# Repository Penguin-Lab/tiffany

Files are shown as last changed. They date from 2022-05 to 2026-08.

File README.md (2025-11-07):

# tiffany
A Tiffany é uma hexapod desenvolvida para andar de forma autônoma ou para ser controlada pelo celular. Para se locomover, ela possui 6 patas de 3 graus de liberdade cada (3 motores) e uma ESP32 que comanda o conjunto! Ela é a segunda integrante robótica do nosso espaço inteligente!

# Estrutura física
A estrutura física do robô é composta por seis patas de três eixos cada (três motores). As patas são fixadas a duas placas de PLA para deixar o robô firme. As peças são todas projetadas em 3D e foram impressas utilizando PLA, podendo ser encontradas na pasta Pecas_3d deste projeto.

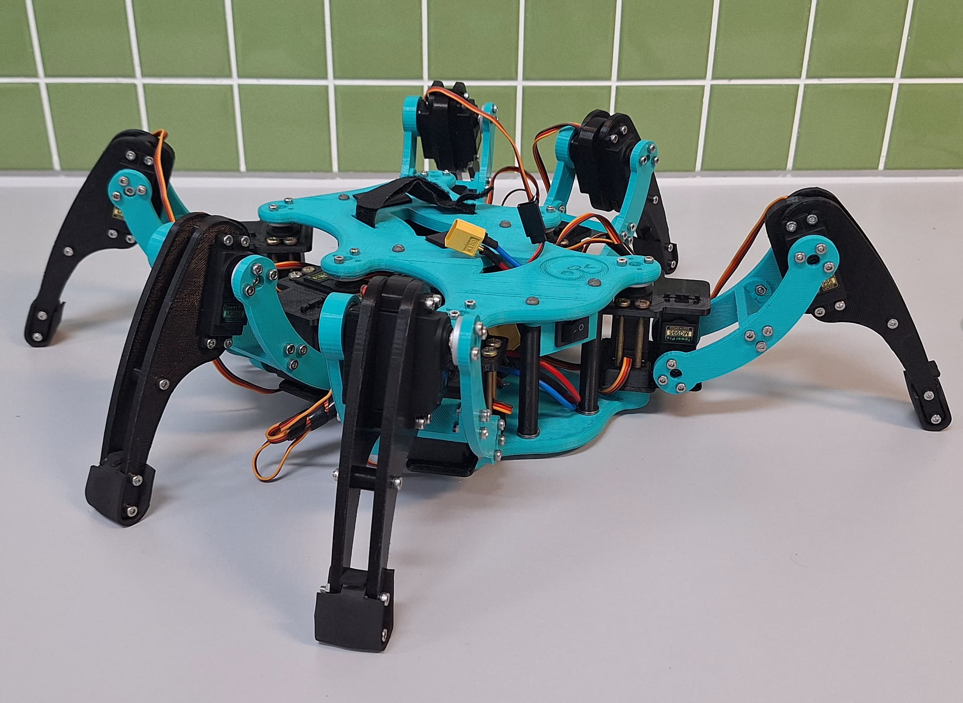
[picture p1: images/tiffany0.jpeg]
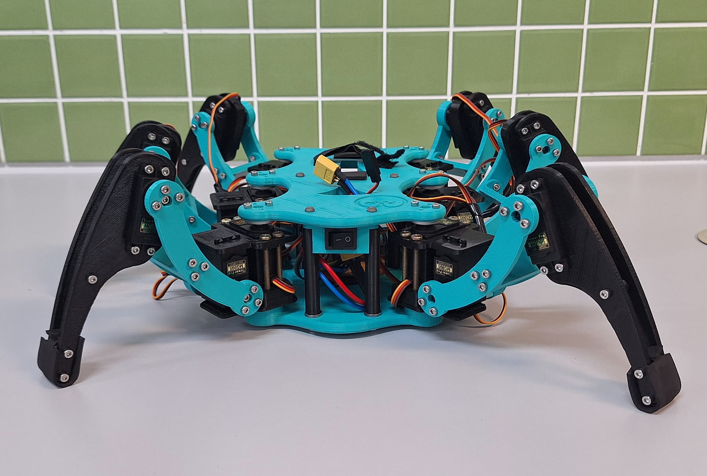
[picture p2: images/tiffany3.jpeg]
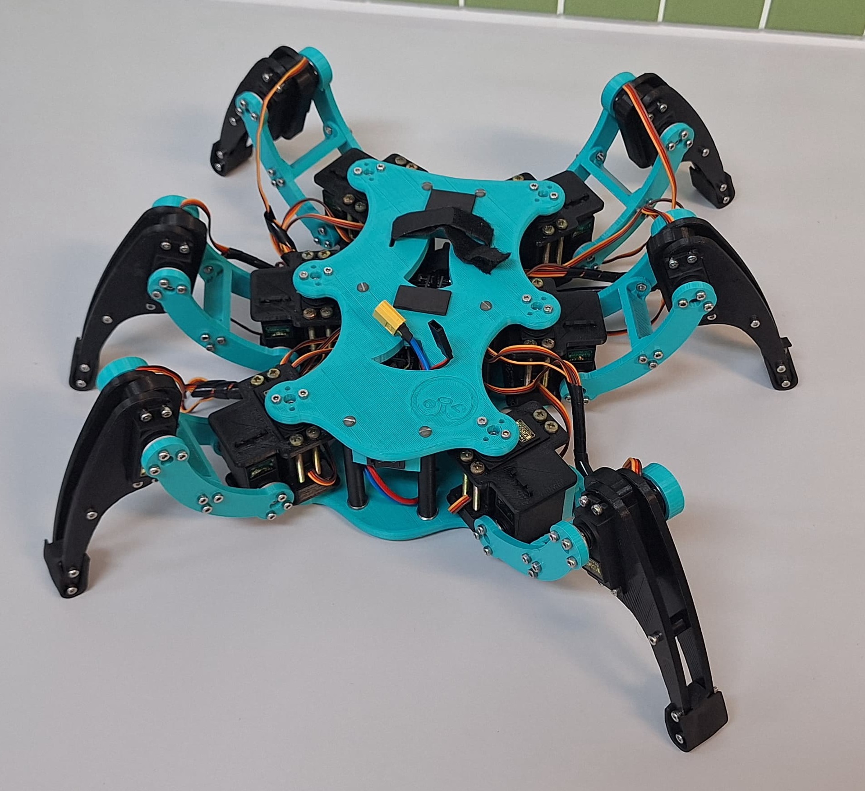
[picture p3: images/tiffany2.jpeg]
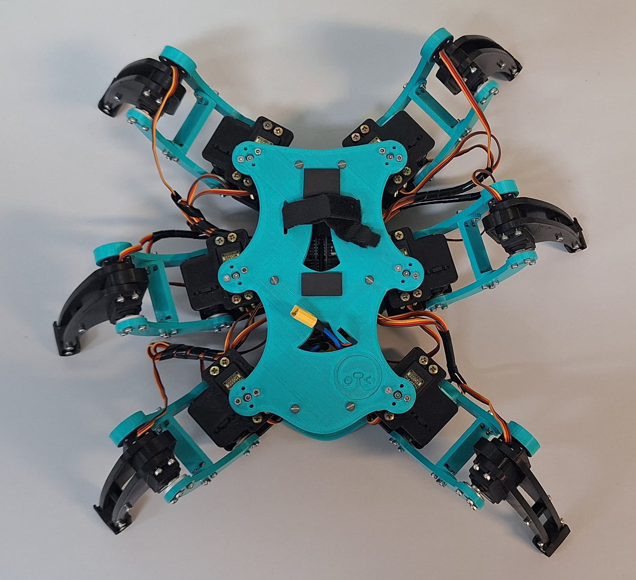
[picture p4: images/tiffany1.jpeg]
   

## Peças 3D em STL
As peças em 3D desenvolvidas para este projeto foram baseadas no projeto do hexapod Steve da Eng. Eletricista Bruna Reis Lyra. Na pasta Pecas_3d, é possível encontrar duas versões dessas peças em STL: uma desenhada para o motor servo TowerPro MG995 (v1) e outra para o DS3230 (v2). Para ajudar, segue abaixo uma lista de todas as peças que devem ser impressas e qual o valor da sua maior dimensão (para ajudar na escolha da impressora):

### V1: Versão para o motor servo TowerPro MG995 
* Corpo
  * 1x [TIFFANY_BODY_DOWN.STL (230 mm)](https://github.com/Penguin-Lab/tiffany/blob/main/Pecas_3d/v1/TIFFANY_BODY_DOWN.STL)
  * 1x [TIFFANY_BODY_UP.STL (230 mm)](https://github.com/Penguin-Lab/tiffany/blob/main/Pecas_3d/v1/TIFFANY_BODY_UP.STL)
  * 6x [TIFFANY_SPACER.STL (68 mm)](https://github.com/Penguin-Lab/tiffany/blob/main/Pecas_3d/v1/TIFFANY_SPACER.STL)
  * 1x [TIFFANY_SUPPORT_PCI.STL (120 mm)](https://github.com/Penguin-Lab/tiffany/blob/main/Pecas_3d/v1/TIFFANY_SUPPORT_PCI.STL)
  * 1x [TIFFANY_SUPPORT_SWITCH.STL (50 mm)](https://github.com/Penguin-Lab/tiffany/blob/main/Pecas_3d/v1/TIFFANY_SUPPORT_SWITCH.STL)
* Patas
  * 6x [TIFFANY_TIBIA_LEFT.STL (141 mm)](https://github.com/Penguin-Lab/tiffany/blob/main/Pecas_3d/v1/TIFFANY_TIBIA_LEFT.STL)
  * 6x [TIFFANY_TIBIA_LEFT.STL espelhado (141 mm)](https://github.com/Penguin-Lab/tiffany/blob/main/Pecas_3d/v1/TIFFANY_TIBIA_LEFT.STL)
  * 6x [TIFFANY_TIBIA_MIDDLE.STL (63 mm)](https://github.com/Penguin-Lab/tiffany/blob/main/Pecas_3d/v1/TIFFANY_TIBIA_MIDDLE.STL)
  * 6x [TIFFANY_TIBIA_TUBO.STL (10 mm)](https://github.com/Penguin-Lab/tiffany/blob/main/Pecas_3d/v1/TIFFANY_TIBIA_TUBO.STL)
  * 6x [TIFFANY_FOOT.STL (25 mm)](https://github.com/Penguin-Lab/tiffany/blob/main/Pecas_3d/v1/TIFFANY_FOOT.STL)
  * 3x [TIFFANY_FEMUR_FRONT.STL (110 mm)](https://github.com/Penguin-Lab/tiffany/blob/main/Pecas_3d/v1/TIFFANY_FEMUR_FRONT.STL)
  * 3x [TIFFANY_FEMUR_BACK.STL (118 mm)](https://github.com/Penguin-Lab/tiffany/blob/main/Pecas_3d/v1/TIFFANY_FEMUR_BACK.STL)
  * 3x [TIFFANY_FEMUR_FRONT.STL espelhado (110 mm)](https://github.com/Penguin-Lab/tiffany/blob/main/Pecas_3d/v1/TIFFANY_FEMUR_FRONT.STL)
  * 3x [TIFFANY_FEMUR_BACK.STL espelhado (118 mm)](https://github.com/Penguin-Lab/tiffany/blob/main/Pecas_3d/v1/TIFFANY_FEMUR_BACK.STL)
  * 6x [TIFFANY_FEMUR_MIDDLE.STL (51 mm)](https://github.com/Penguin-Lab/tiffany/blob/main/Pecas_3d/v1/TIFFANY_FEMUR_MIDDLE.STL)
  * 6x [TIFFANY_OMBRO_UP.STL (61 mm)](https://github.com/Penguin-Lab/tiffany/blob/main/Pecas_3d/v1/TIFFANY_OMBRO_UP.STL)
  * 3x [TIFFANY_OMBRO_DOWN_LEFT.STL (61 mm)](https://github.com/Penguin-Lab/tiffany/blob/main/Pecas_3d/v1/TIFFANY_OMBRO_DOWN_LEFT.STL)
  * 3x [TIFFANY_OMBRO_DOWN_LEFT.STL espelhado (61 mm)](https://github.com/Penguin-Lab/tiffany/blob/main/Pecas_3d/v1/TIFFANY_OMBRO_DOWN_LEFT.STL)
* Motor
  * 12x [TIFFANY_TAMPA_MOTOR.STL (41 mm)](https://github.com/Penguin-Lab/tiffany/blob/main/Pecas_3d/v1/TIFFANY_TAMPA_MOTOR.STL)

Obs: a tampa de 12 motores deverão ser trocadas pelas peças [TIFFANY_TAMPA_MOTOR.STL](https://github.com/Penguin-Lab/tiffany/blob/main/Pecas_3d/v1/TIFFANY_TAMPA_MOTOR.STL) para que seja possível fixar os rolamentos nas patas. Serão utilizados 3 rolamentos por pata:

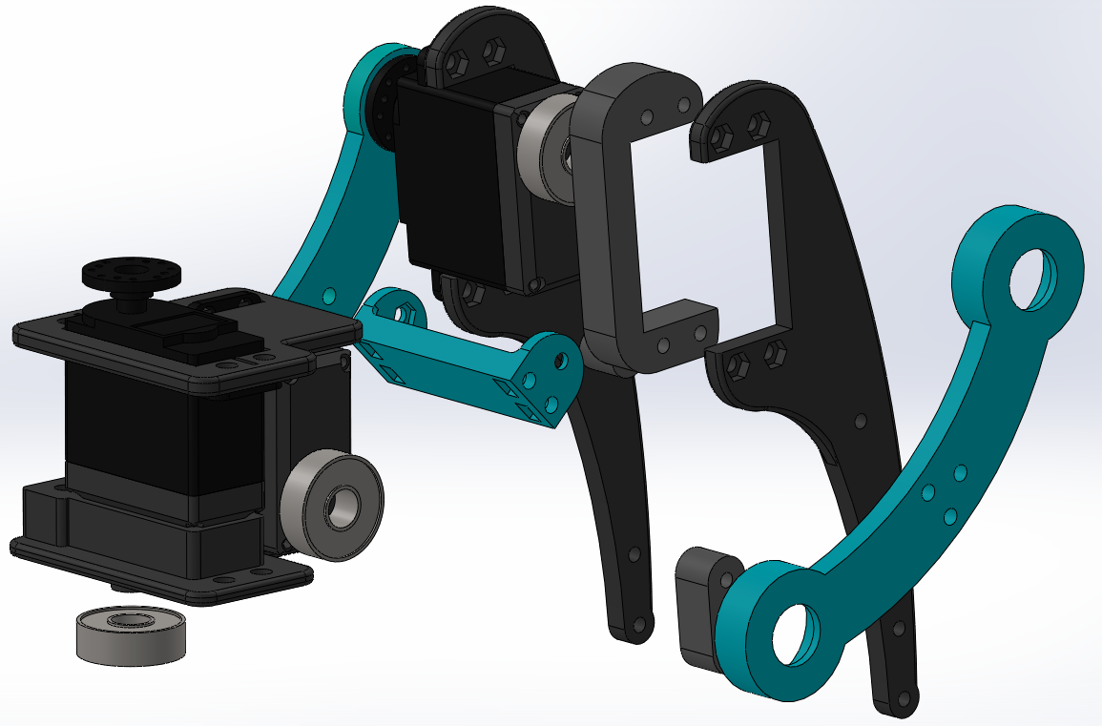
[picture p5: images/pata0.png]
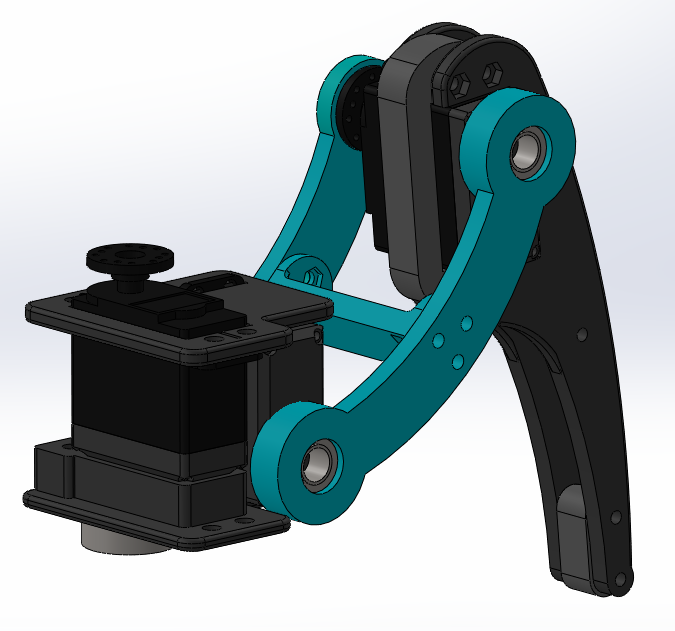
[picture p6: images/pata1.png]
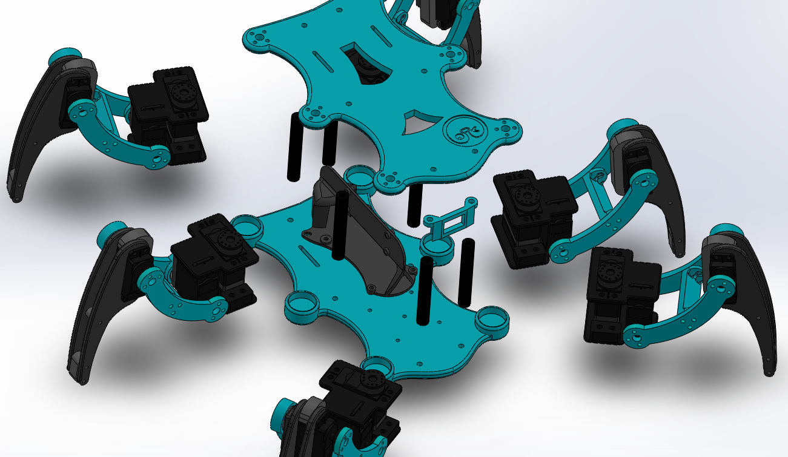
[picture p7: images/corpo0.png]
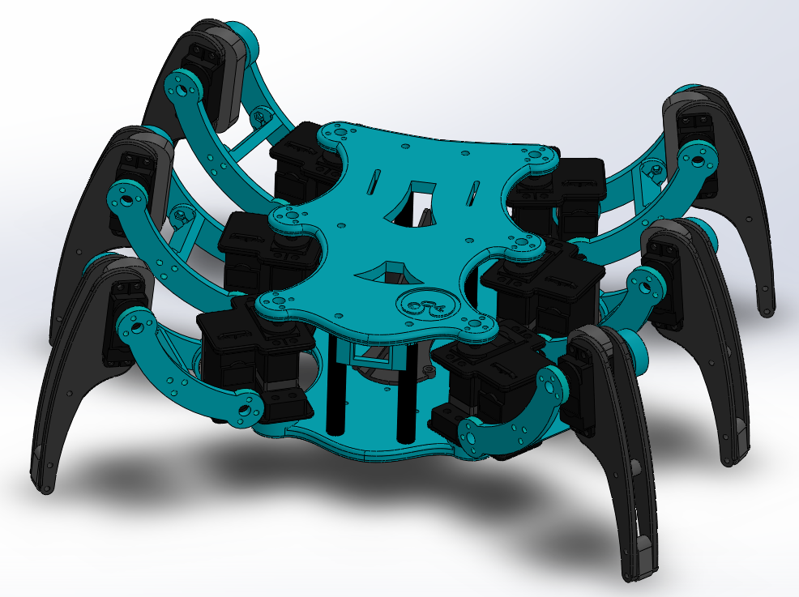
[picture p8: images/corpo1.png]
   

### V2: Versão para o motor servo DS3230 PRO-180 
* Corpo
  * 1x [TIFFANY_BODY_DOWN.STL (230 mm)](https://github.com/Penguin-Lab/tiffany/blob/main/Pecas_3d/v2/TIFFANY_BODY_DOWN.STL)
  * 1x [TIFFANY_BODY_UP.STL (230 mm)](https://github.com/Penguin-Lab/tiffany/blob/main/Pecas_3d/v2/TIFFANY_BODY_UP.STL)
  * 2x [TIFFANY_SPACER.STL (67 mm)](https://github.com/Penguin-Lab/tiffany/blob/main/Pecas_3d/v2/TIFFANY_SPACER.STL)
  * 4x [TIFFANY_SPACER_FRONT.STL (63 mm)](https://github.com/Penguin-Lab/tiffany/blob/main/Pecas_3d/v2/TIFFANY_SPACER_FRONT.STL)
  * 1x [TIFFANY_SUPORT_PCI.STL (120 mm)](https://github.com/Penguin-Lab/tiffany/blob/main/Pecas_3d/v2/TIFFANY_SUPORT_PCI.STL)
  * 1x [TIFFANY_SUPORT_SWITCH.STL (50 mm)](https://github.com/Penguin-Lab/tiffany/blob/main/Pecas_3d/v2/TIFFANY_SUPORT_SWITCH.STL)
  * 1x [TIFFANY_SUPORT_BATTERY_PLUG.STL (44 mm)](https://github.com/Penguin-Lab/tiffany/blob/main/Pecas_3d/v2/TIFFANY_SUPORT_BATTERY_PLUG.STL)
  * 1x [TIFFANY_LOGO.STL (36 mm)](https://github.com/Penguin-Lab/tiffany/blob/main/Pecas_3d/v2/TIFFANY_LOGO.STL)
* Patas
  * 6x [TIFFANY_TIBIA_LEFT.STL (141 mm)](https://github.com/Penguin-Lab/tiffany/blob/main/Pecas_3d/v2/TIFFANY_TIBIA_LEFT.STL)
  * 6x [TIFFANY_TIBIA_LEFT.STL espelhado (141 mm)](https://github.com/Penguin-Lab/tiffany/blob/main/Pecas_3d/v2/TIFFANY_TIBIA_LEFT.STL)
  * 6x [TIFFANY_TIBIA_MIDDLE.STL (63 mm)](https://github.com/Penguin-Lab/tiffany/blob/main/Pecas_3d/v2/TIFFANY_TIBIA_MIDDLE.STL)
  * 6x [TIFFANY_TIBIA_TUBO.STL (10 mm)](https://github.com/Penguin-Lab/tiffany/blob/main/Pecas_3d/v2/TIFFANY_TIBIA_TUBO.STL)
  * 6x [TIFFANY_FOOT.STL (25 mm)](https://github.com/Penguin-Lab/tiffany/blob/main/Pecas_3d/v2/TIFFANY_FOOT.STL)
  * 3x [TIFFANY_FEMUR_FRONT.STL (110 mm)](https://github.com/Penguin-Lab/tiffany/blob/main/Pecas_3d/v2/TIFFANY_FEMUR_FRONT.STL)
  * 3x [TIFFANY_FEMUR_BACK.STL (118 mm)](https://github.com/Penguin-Lab/tiffany/blob/main/Pecas_3d/v2/TIFFANY_FEMUR_BACK.STL)
  * 3x [TIFFANY_FEMUR_FRONT.STL espelhado (110 mm)](https://github.com/Penguin-Lab/tiffany/blob/main/Pecas_3d/v2/TIFFANY_FEMUR_FRONT.STL)
  * 3x [TIFFANY_FEMUR_BACK.STL espelhado (118 mm)](https://github.com/Penguin-Lab/tiffany/blob/main/Pecas_3d/v2/TIFFANY_FEMUR_BACK.STL)
  * 6x [TIFFANY_FEMUR_MIDDLE.STL (51 mm)](https://github.com/Penguin-Lab/tiffany/blob/main/Pecas_3d/v2/TIFFANY_FEMUR_MIDDLE.STL)
  * 6x [TIFFANY_OMBRO_UP.STL (61 mm)](https://github.com/Penguin-Lab/tiffany/blob/main/Pecas_3d/v2/TIFFANY_OMBRO_UP.STL)
  * 3x [TIFFANY_OMBRO_DOWN_LEFT.STL (61 mm)](https://github.com/Penguin-Lab/tiffany/blob/main/Pecas_3d/v2/TIFFANY_OMBRO_DOWN_LEFT.STL)
  * 3x [TIFFANY_OMBRO_DOWN_LEFT.STL espelhado (61 mm)](https://github.com/Penguin-Lab/tiffany/blob/main/Pecas_3d/v2/TIFFANY_OMBRO_DOWN_LEFT.STL)
* Motor
  * 12x [TIFFANY_TAMPA_MOTOR_DS3230.STL (41 mm)](https://github.com/Penguin-Lab/tiffany/blob/main/Pecas_3d/v2/TIFFANY_TAMPA_MOTOR_DS3230.STL)

Obs: no caso do DS3230, a tampa de 12 motores deverão ser trocadas pelas peças [TIFFANY_TAMPA_MOTOR_DS3230.STL](https://github.com/Penguin-Lab/tiffany/blob/main/Pecas_3d/v2/TIFFANY_TAMPA_MOTOR_DS3230.STL) para que seja possível fixar os rolamentos nas patas. Serão utilizados 3 rolamentos por pata.

## Outros itens da estrutura
Alguns outros itens são necessários para finalizar a estrutura da Tiffany:
* 6x Parafusos m4 ou similar de cm: prender as peças [TIFFANY_BODY_UP.STL](https://github.com/Penguin-Lab/tiffany/blob/main/Pecas_3d/TIFFANY_BODY_UP.STL) e [TIFFANY_BODY_DOWN.STL](https://github.com/Penguin-Lab/tiffany/blob/main/Pecas_3d/TIFFANY_BODY_DOWN.STL)
* 24x Parafusos m4 de cm: prender as peças [TIFFANY_OMBRO_DOWN_LEFT.STL](https://github.com/Penguin-Lab/tiffany/blob/main/Pecas_3d/TIFFANY_OMBRO_DOWN_LEFT.STL) e [TIFFANY_OMBRO_UP.STL](https://github.com/Penguin-Lab/tiffany/blob/main/Pecas_3d/TIFFANY_OMBRO_UP.STL)
* 24x Parafusos m3 de cm: prender as peças [TIFFANY_TIBIA_LEFT.STL](https://github.com/Penguin-Lab/tiffany/blob/main/Pecas_3d/TIFFANY_TIBIA_LEFT.STL) nos motores
* 6x Tiras de EVA: colocar na ponta das peças [TIFFANY_FOOT.STL](https://github.com/Penguin-Lab/tiffany/blob/main/Pecas_3d/TIFFANY_FOOT.STL) para evitar que o robô deslize
* Arruelas entre as peças [TIFFANY_SPACER.STL](https://github.com/Penguin-Lab/tiffany/blob/main/Pecas_3d/TIFFANY_SPACER.STL) e [TIFFANY_BODY_UP.STL](https://github.com/Penguin-Lab/tiffany/blob/main/Pecas_3d/TIFFANY_BODY_UP.STL) para ajustar a altura correta do interior do robô

## Placa de circuito impresso
No projeto, foi desenvolvida uma placa de circuito para servir como shield para a ESP32 e conexão com as duas placas PCA9685.

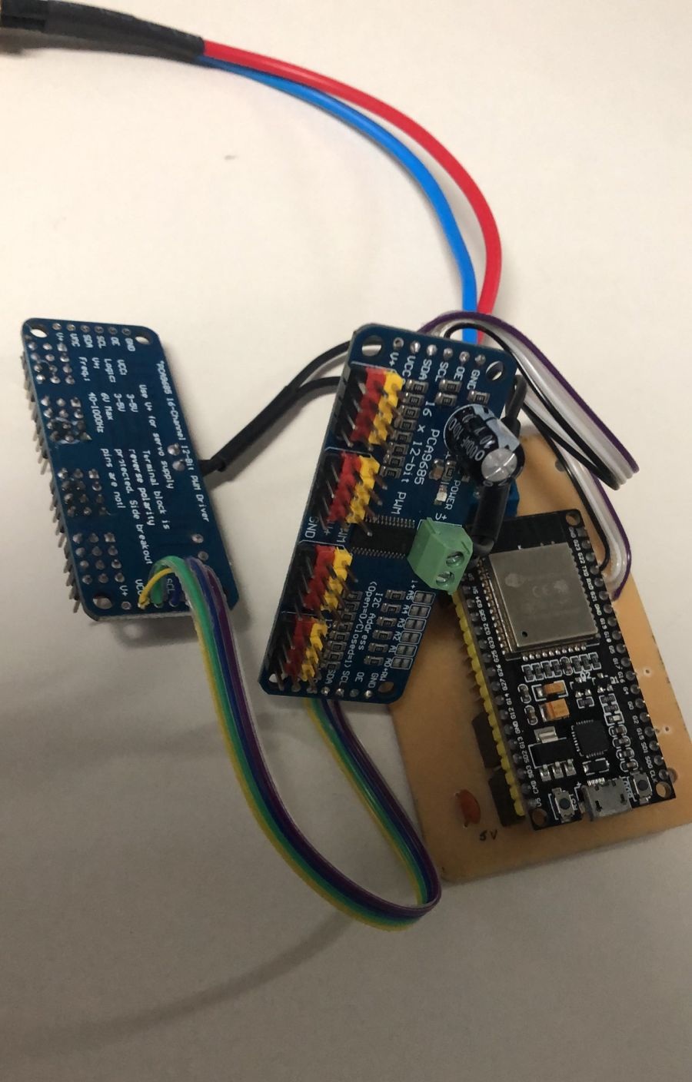
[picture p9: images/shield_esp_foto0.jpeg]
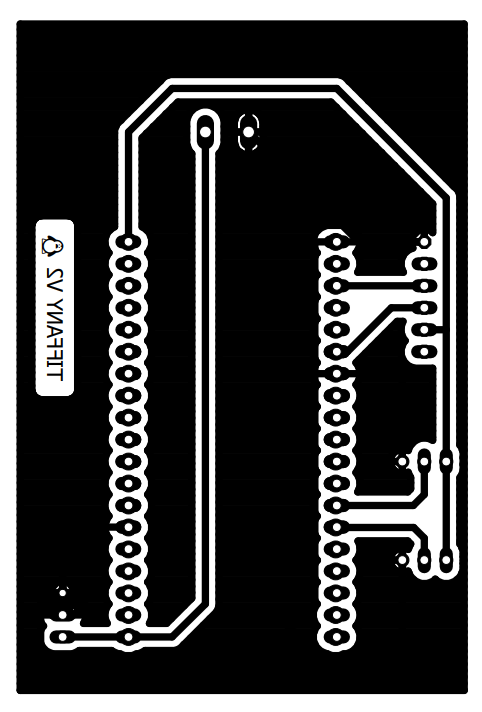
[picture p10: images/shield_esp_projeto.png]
 

## Calibração dos motores
A calibração dos motores é feita utilizando o [CALIBRADOR DE MOTORES](https://github.com/Penguin-Lab/calib_servomotor) conectado às PCAs da Tiffany. Isso deve ser feito pelo clock das PCAs ser diferente de uma placa para outra. Logo, os motores da esquerda são calibrados utilizando a PCA da esquerda e os da direita com a PCA da direita. Os valores retornados pela calibração são jogados nesta [PLANILHA](https://docs.google.com/spreadsheets/d/1Kh9AVbb79lXnJq5dlCiB7NEVVmcJWRX6X2CdDR9_QZo/edit?usp=sharing). A planilha ajeita os valores de PWM retornados na IDE do Arduino para valores que representem 0 e 180 graus dos motores já na estrutura das patas. Esses valores são os mesmos listados no código de comando da Tiffany.

## Componentes eletrônicos
Os componentes eletrônicos embarcados no robô e equipamentos utilizados estão listados abaixo.
### V1: Versão para o motor servo TowerPro MG995 
* Controlador com Wi-fi e Bluetooth
  * 1x ESP32 (38 pinos)
* Motores
  * 18x Servo TowerPro MG995 Metálico
* 2x Placas PCA9685 para comando dos 18 motores (9 motores em cada)
* Chave (switch)
* Alimentação
  * Bateria Zippy LiFe 1100mAh 2s 6,6V (ESP32)
  * Bateria TM Hobbies LiFe 2100mAh 2s 6,6v (motores)

### V2: Versão para o motor servo DS3230 PRO-180 
* Controlador com Wi-fi e Bluetooth
  * 1x ESP32 (38 pinos)
* Motores
  * 18x Servo DS3230 PRO-180
* 2x Placas PCA9685 para comando dos 18 motores (9 motores em cada)
* Chave (switch)
* Chave pequena (switch)
* Alimentação
  * Regulador para 5V (ESP32)
  * Regulador HV SBEC YPG 20A configurado para saída de 6V (motores)
  * Bateria LiPo 5000mAh 3s 11,1V (motores)

# Software
Na pasta de códigos, há dois códigos de programação da ESP32 (38 pinos). Eles são exemplos em C++ do comando de movimentação da Tiffany:
* Dabble: a ESP32 pode se comunicar com o aplicativo Dabble no celular e receber comandos de ação;
* Espaço Inteligente (IS): a ESP32 pode se comunicar com o Espaço Inteligente e receber esses mesmos comandos.

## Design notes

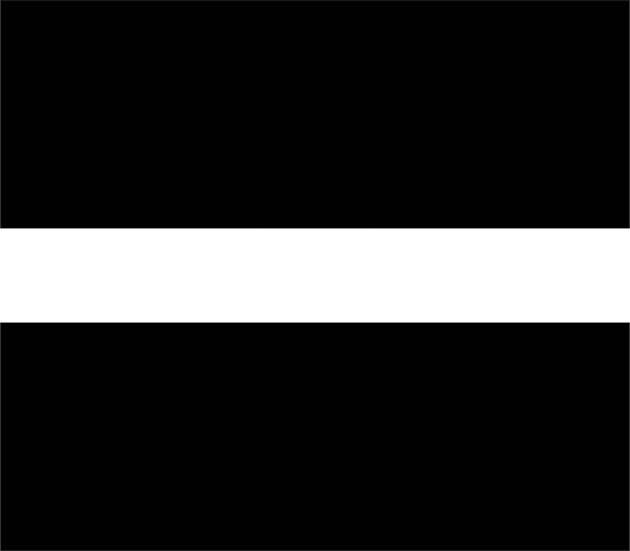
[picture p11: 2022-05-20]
images/shield_esp_cut.png

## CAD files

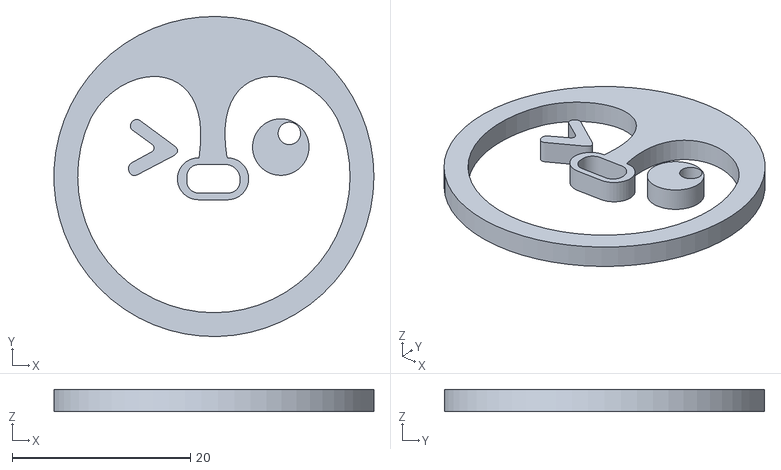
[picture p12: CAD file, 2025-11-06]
Pecas_3d/v2/TIFFANY_LOGO.STL
35.9 x 35.9 x 2.50

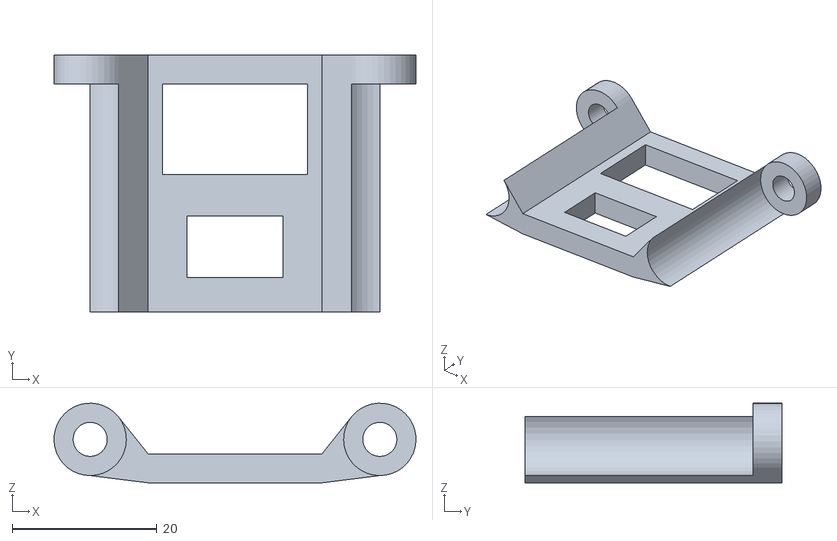
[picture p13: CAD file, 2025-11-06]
Pecas_3d/v2/TIFFANY_SUPORT_SWITCH.STL
50.0 x 35.5 x 11.0

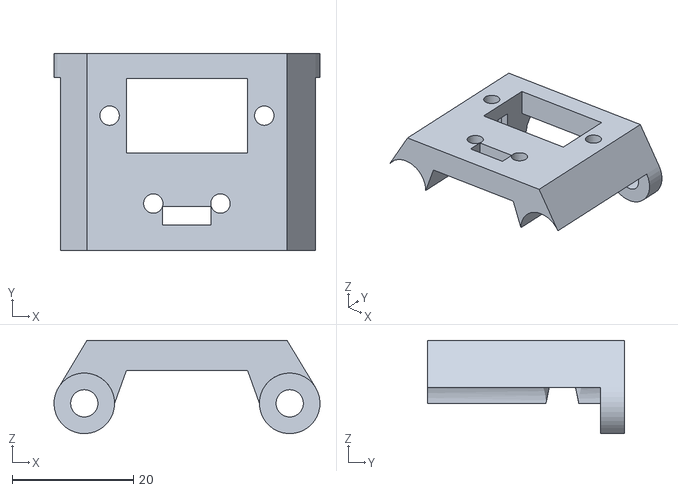
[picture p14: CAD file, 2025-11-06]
Pecas_3d/v2/TIFFANY_SUPORT_BATTERY_PLUG.STL
43.9 x 32.5 x 15.4

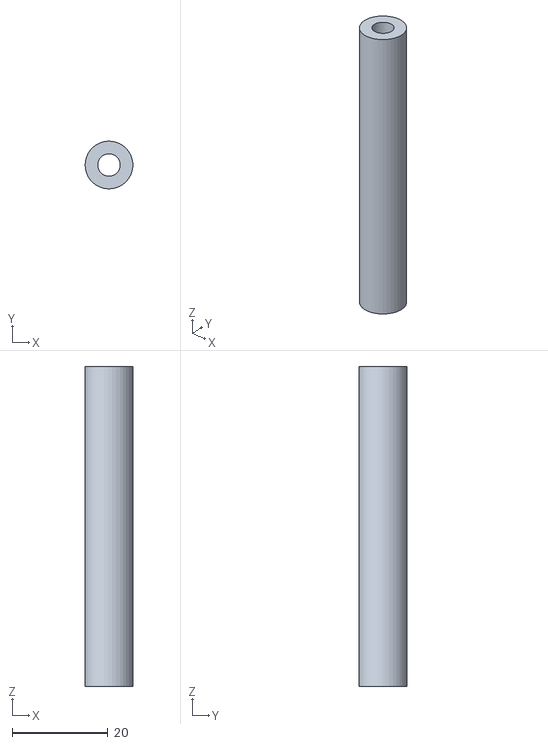
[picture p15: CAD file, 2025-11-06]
Pecas_3d/v2/TIFFANY_SPACER.STL
10.0 x 9.99 x 67.0

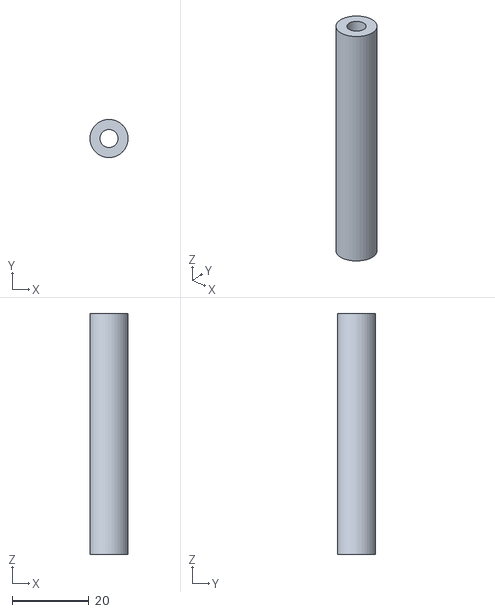
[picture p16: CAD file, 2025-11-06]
Pecas_3d/v2/TIFFANY_SPACER_FRONT.STL
10.0 x 9.99 x 63.0

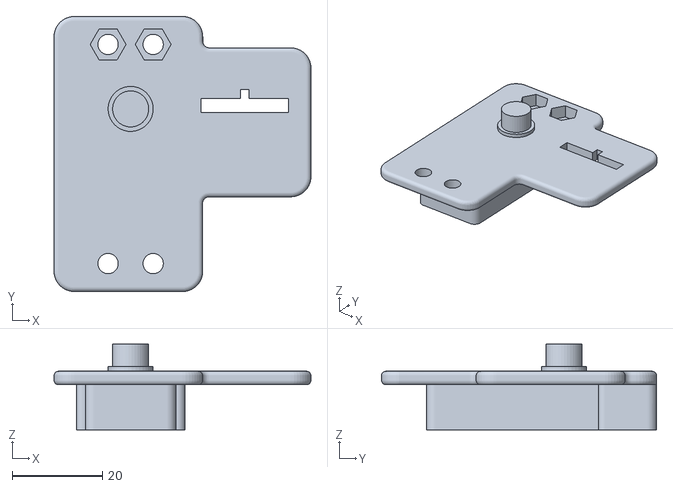
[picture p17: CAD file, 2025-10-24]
Pecas_3d/v2/TIFFANY_OMBRO_DOWN_LEFT.STL
57.0 x 61.0 x 19.0

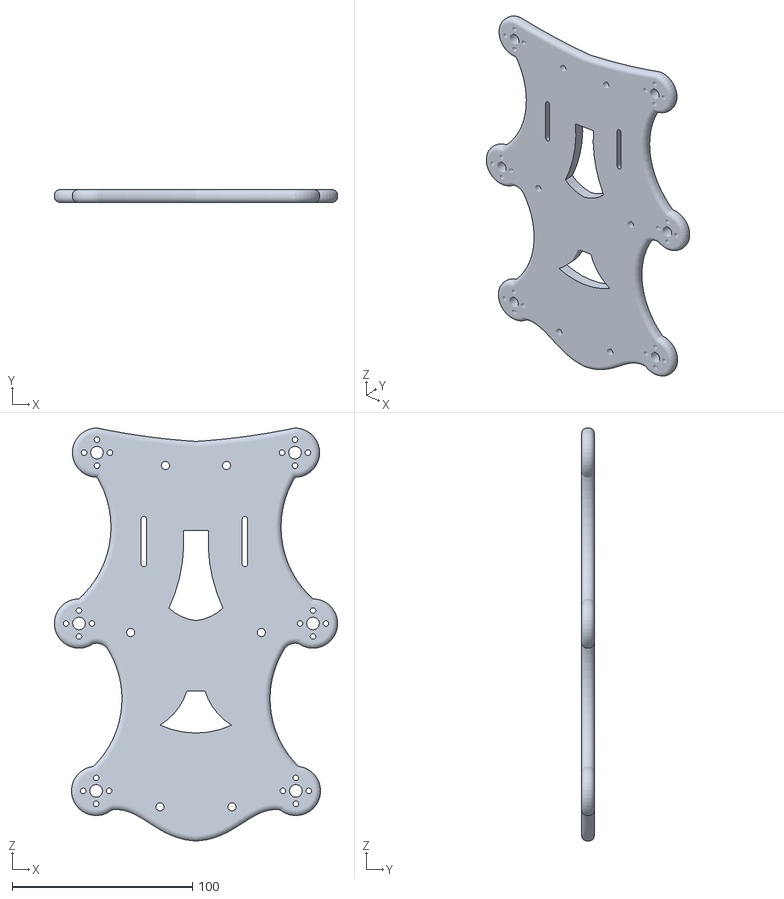
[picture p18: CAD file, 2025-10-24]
Pecas_3d/v2/TIFFANY_BODY_UP.STL
157.4 x 7.00 x 229.4

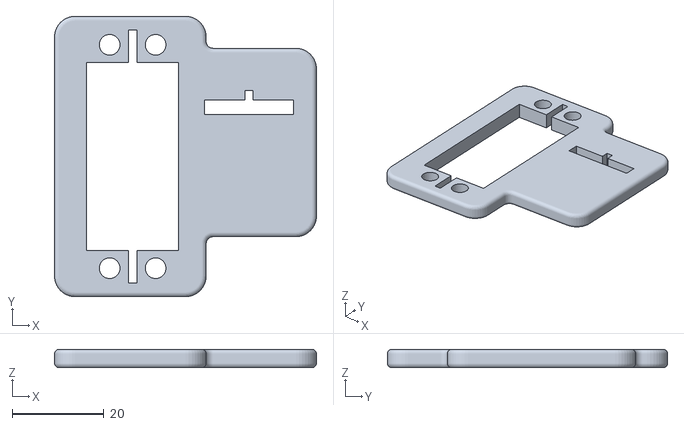
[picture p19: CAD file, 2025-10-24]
Pecas_3d/v2/TIFFANY_OMBRO_UP.STL
57.0 x 61.0 x 4.00

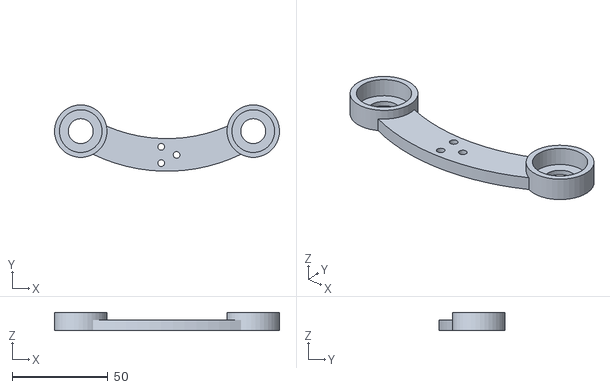
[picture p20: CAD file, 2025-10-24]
Pecas_3d/v2/TIFFANY_FEMUR_BACK.STL
117.4 x 34.6 x 9.50

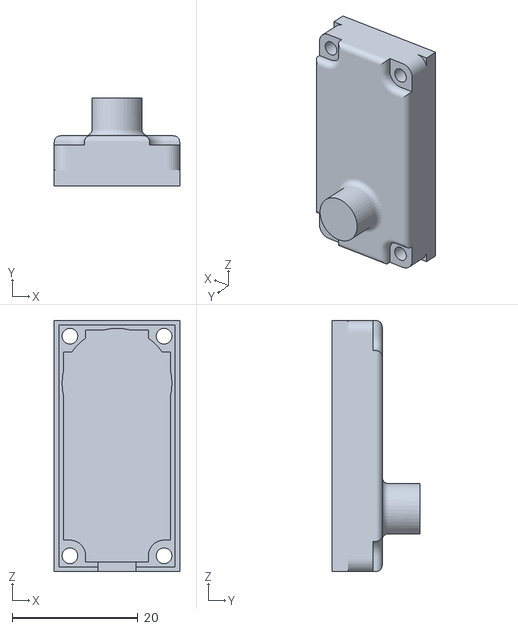
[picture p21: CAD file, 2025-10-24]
Pecas_3d/v2/TIFFANY_TAMPA_MOTOR_DS3230.STL
20.0 x 14.0 x 40.0

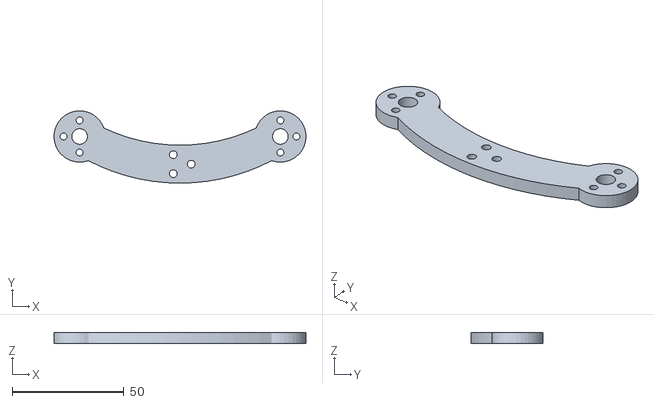
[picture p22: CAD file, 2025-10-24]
Pecas_3d/v2/TIFFANY_FEMUR_FRONT.STL
113.0 x 32.4 x 5.00

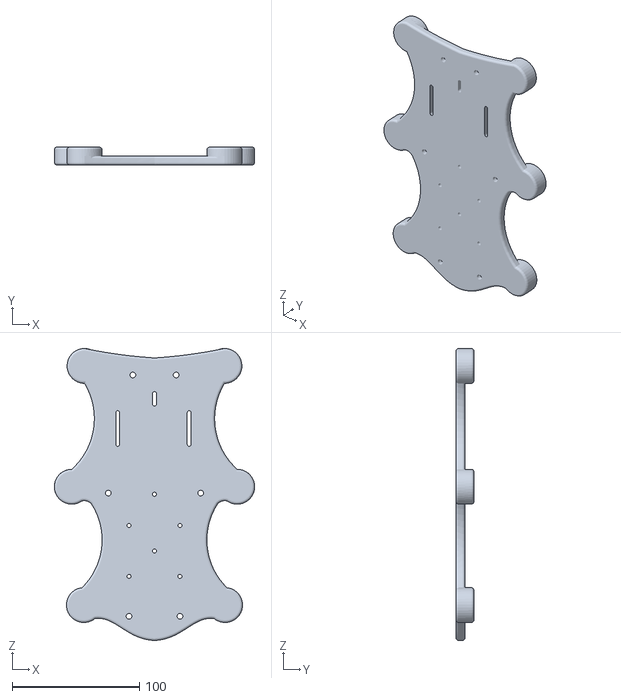
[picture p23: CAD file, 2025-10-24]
Pecas_3d/v2/TIFFANY_BODY_DOWN.STL
157.4 x 14.0 x 229.4

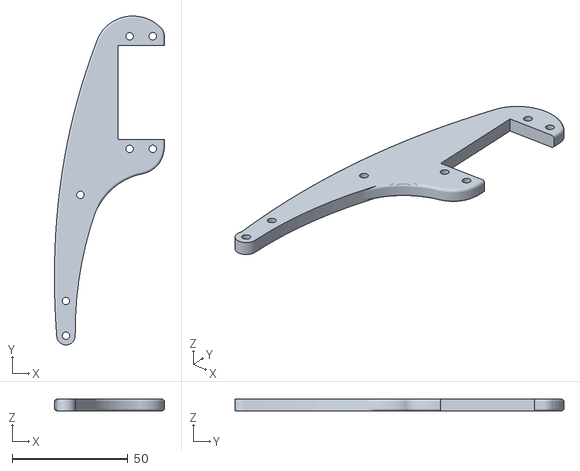
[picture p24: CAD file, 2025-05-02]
Pecas_3d/v2/TIFFANY_TIBIA_LEFT.STL
47.5 x 142.0 x 5.00

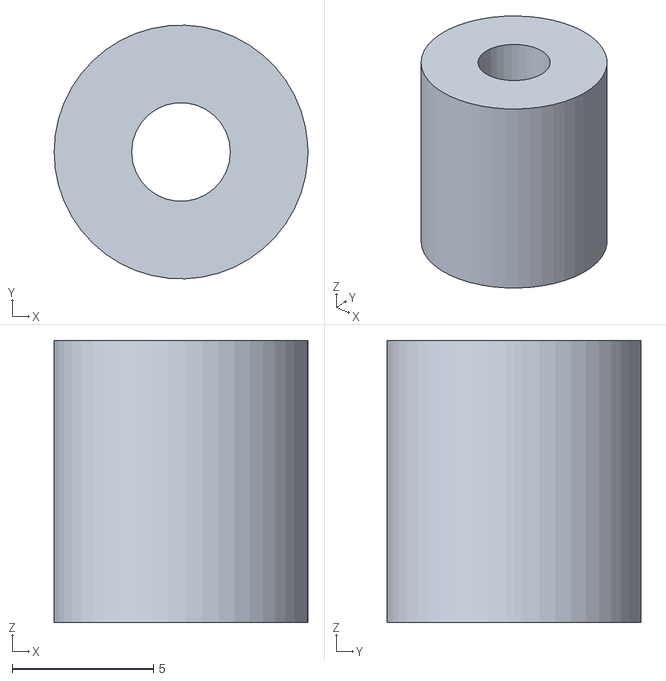
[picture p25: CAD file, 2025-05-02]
Pecas_3d/v2/TIFFANY_TIBIA_TUBO.STL
9.00 x 8.99 x 10.0

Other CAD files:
Pecas_3d/v2/TIFFANY_SUPORT_PCI.STL
Pecas_3d/v2/TIFFANY_FEMUR_MIDDLE.STL
Pecas_3d/v2/TIFFANY_TIBIA_MIDDLE.STL
Pecas_3d/v2/TIFFANY_FOOT.STL
Pecas_3d/v1/MONTAGEM.STL
Pecas_3d/v1/TIFFANY_BODY_DOWN.STL
Pecas_3d/v1/TIFFANY_BODY_UP.STL
Pecas_3d/v1/TIFFANY_FEMUR_BACK.STL
Pecas_3d/v1/TIFFANY_FEMUR_FRONT.STL
Pecas_3d/v1/TIFFANY_OMBRO_DOWN_LEFT.STL
Pecas_3d/v1/TIFFANY_OMBRO_UP.STL
Pecas_3d/v1/TIFFANY_SPACER.STL
Pecas_3d/v1/TIFFANY_TAMPA_MOTOR.STL

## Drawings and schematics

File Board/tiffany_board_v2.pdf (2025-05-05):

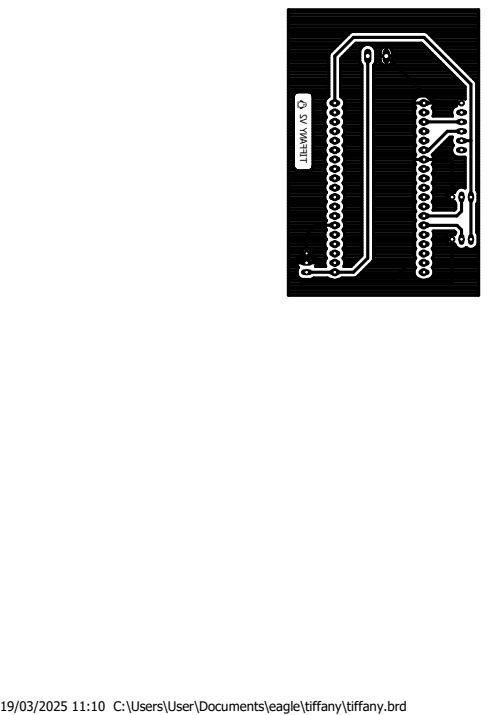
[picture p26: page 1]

19/03/2025 11:10 C:\Users\User\Documents\eagle\tiffany\tiffany.brd TIFFANY V2

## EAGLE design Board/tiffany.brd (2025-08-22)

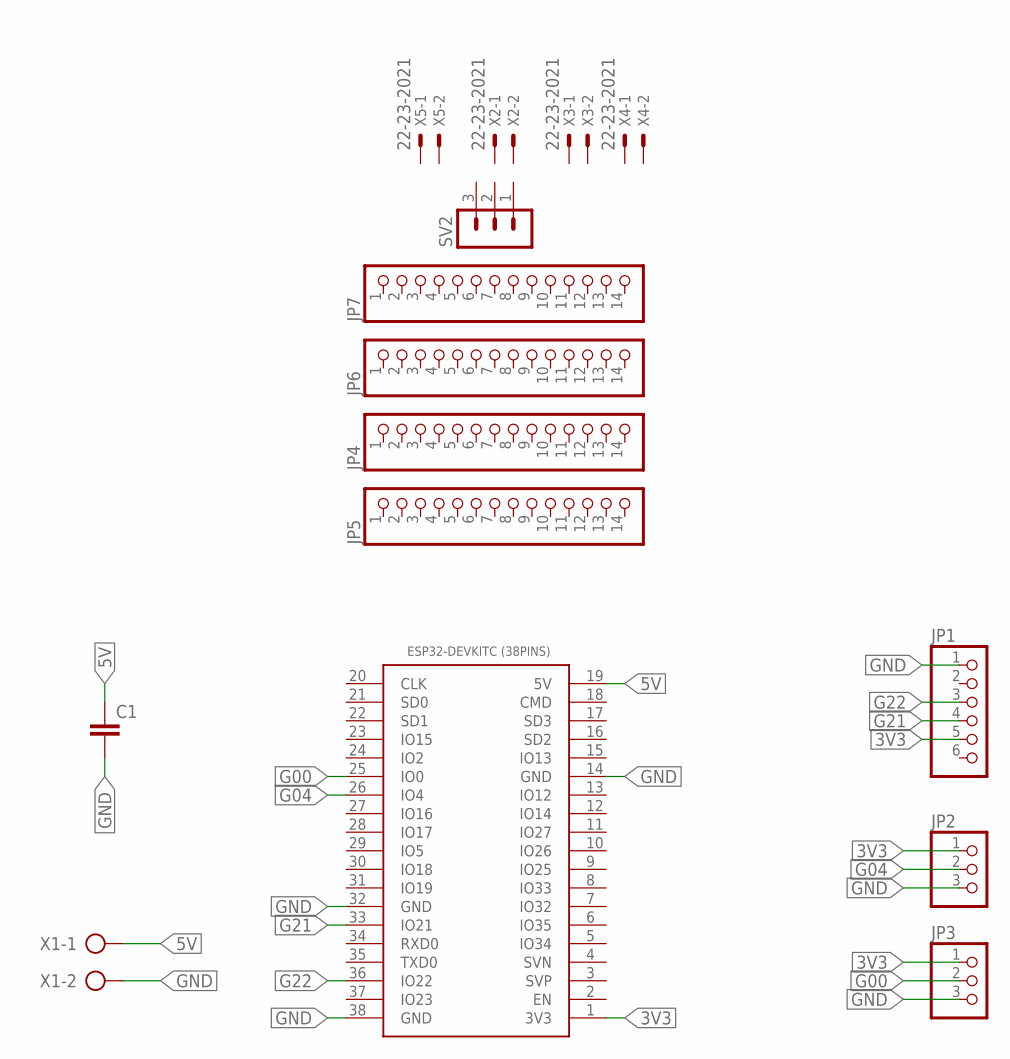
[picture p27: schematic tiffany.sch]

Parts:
C1: C-EU050-024X044; C050-024X044
ESP32-DEVKITC(38PINS)1: ESP32DEVKITC_38PINS; ESP32-DEVKITC
JP1: PINHD-1X6; 1X06
JP2, JP3: PINHD-1X3; 1X03
JP4, JP5, JP6, JP7: PINHD-1X14; 1X14
SV2: MA03-1
X1: AK300/2
X2, X3, X4, X5: 22-23-2021

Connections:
3V3: ESP32-DEVKITC(38PINS)1.1 (3V3), JP1.5, JP2.1, JP3.1
5V: C1.1, ESP32-DEVKITC(38PINS)1.19 (5V), X1.1
G00: ESP32-DEVKITC(38PINS)1.25 (IO0), JP3.2
G04: ESP32-DEVKITC(38PINS)1.26 (IO4), JP2.2
G21: ESP32-DEVKITC(38PINS)1.33 (IO21), JP1.4
G22: ESP32-DEVKITC(38PINS)1.36 (IO22), JP1.3
GND: C1.2, ESP32-DEVKITC(38PINS)1.14 (GND), ESP32-DEVKITC(38PINS)1.32 (GND), ESP32-DEVKITC(38PINS)1.38 (GND), JP1.1, JP2.3, JP3.3, X1.2

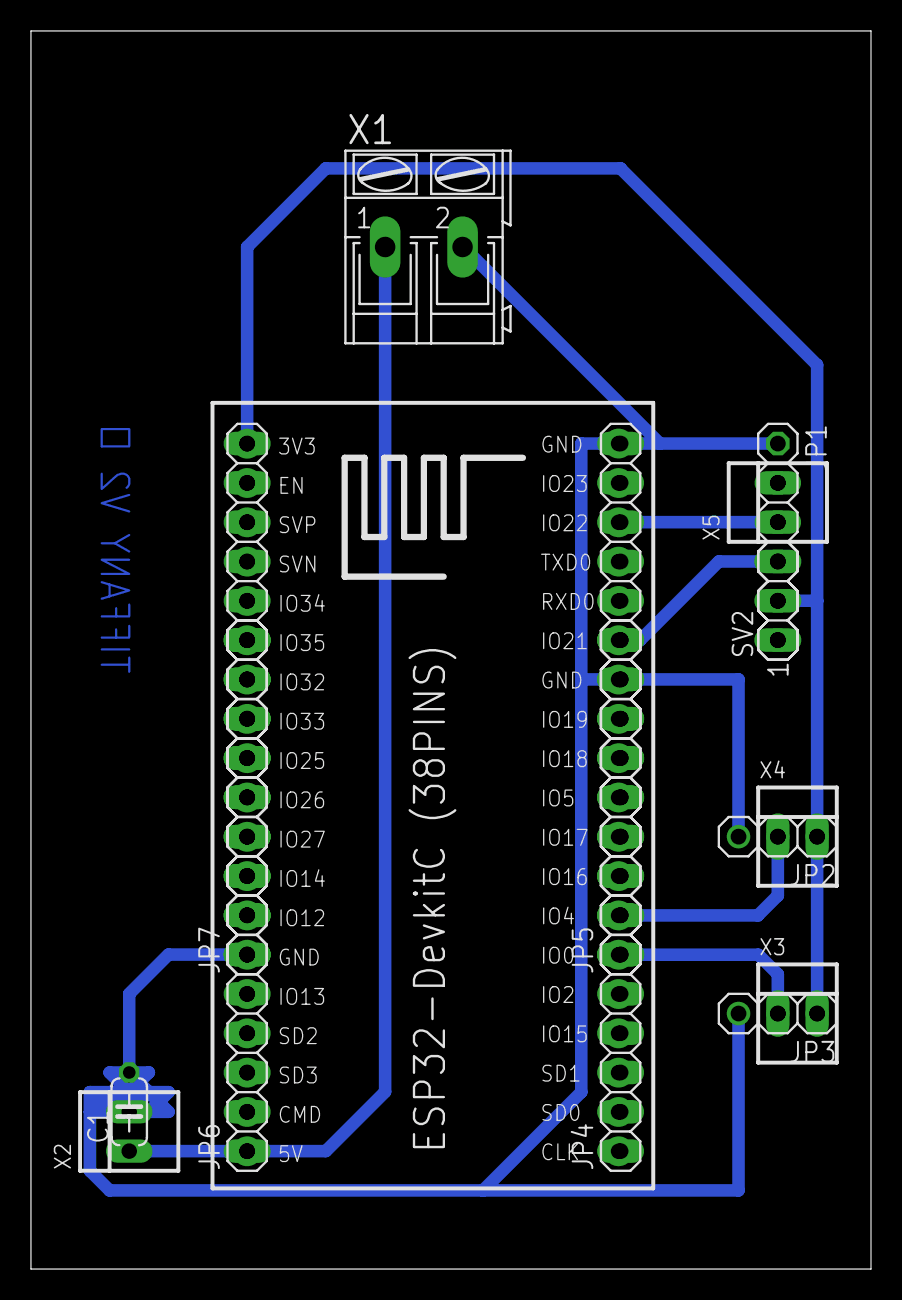
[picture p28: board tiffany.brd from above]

Board: 2 copper layers, 54.3 x 80.0 mm, 15 parts (0 on the bottom side), 7 nets.

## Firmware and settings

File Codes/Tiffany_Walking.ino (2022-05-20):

#define CUSTOM_SETTINGS
#define INCLUDE_GAMEPAD_MODULE
#include <DabbleESP32.h>

// Recommended pins include 2,4,12-19,21-23,25-27,32-33
int tfrPin = 32;
int ffrPin = 33;
int ofrPin = 25;
int tflPin = 23;
int fflPin = 22;
int oflPin = 21;
int tmrPin = 26;
int fmrPin = 27;
int omrPin = 19;
int tmlPin = 18;
int fmlPin = 17;
int omlPin = 16;
int tbrPin = 13;
int fbrPin = 12;
int obrPin = 14;
int tblPin = 15;
int fblPin = 2;
int oblPin = 4;

//Timer Interrupt:
int tbr, tmr, tfr, tbl, tml, tfl; // tibias
int fbr, fmr, ffr, fbl, fml, ffl; // femures
int obr, omr, ofr, obl, oml, ofl; // ombros

int cont = 0;
bool dance = 0;

String txtpwm;

hw_timer_t * timer = NULL;
portMUX_TYPE timerMux = portMUX_INITIALIZER_UNLOCKED;

void IRAM_ATTR onTimer() {
  cont++;
  if(cont > 1000) 
   cont = 0;
   
  if(cont == 0) //tibias direita
   digitalWrite(tbrPin,HIGH);
  else if(cont == (tbr+5)) 
   digitalWrite(tbrPin,LOW);
  if(cont == 0) 
   digitalWrite(tmrPin,HIGH);
  else if(cont == tmr) 
   digitalWrite(tmrPin,LOW);
  if(cont == 0) 
   digitalWrite(tfrPin,HIGH);
  else if(cont == tfr) 
   digitalWrite(tfrPin,LOW);
  
  if(cont == 0) //tibias esquerda
   digitalWrite(tblPin,HIGH);
  else if(cont == (tbl-7)) 
   digitalWrite(tblPin,LOW);
  if(cont == 0) 
   digitalWrite(tmlPin,HIGH);
  else if(cont == (tml-7)) 
   digitalWrite(tmlPin,LOW);
  if(cont == 0) 
   digitalWrite(tflPin,HIGH);
  else if(cont == (tfl-5)) 
   digitalWrite(tflPin,LOW);
    
  if(cont == 0) //femures direita
    digitalWrite(fbrPin,HIGH);
  else if(cont == (fbr+4)) 
    digitalWrite(fbrPin,LOW);
  if(cont == 0) 
    digitalWrite(fmrPin,HIGH);
  else if(cont == fmr) 
    digitalWrite(fmrPin,LOW);
  if(cont == 0) 
    digitalWrite(ffrPin,HIGH);
  else if(cont == ffr) 
    digitalWrite(ffrPin,LOW);

  if(cont == 0) //femures esquerda
    digitalWrite(fblPin,HIGH);
  else if(cont == (fbl-4)) 
    digitalWrite(fblPin,LOW);
  if(cont == 0) 
    digitalWrite(fmlPin,HIGH);
  else if(cont == (fml-6)) 
    digitalWrite(fmlPin,LOW);
  if(cont == 0) 
    digitalWrite(fflPin,HIGH);
  else if(cont == (ffl-6)) 
    digitalWrite(fflPin,LOW);

  if(cont == 0) //ombro direita
    digitalWrite(obrPin,HIGH);
  else if(cont == (obr+2)) 
    digitalWrite(obrPin,LOW);
  if(cont == 0) 
    digitalWrite(omrPin,HIGH);
  else if(cont == omr) 
    digitalWrite(omrPin,LOW);
  if(cont == 0) 
    digitalWrite(ofrPin,HIGH);
  else if(cont == ofr) 
    digitalWrite(ofrPin,LOW);

  if(cont == 0) //ombro esquerda
    digitalWrite(oblPin,HIGH);
  else if(cont == obl) 
    digitalWrite(oblPin,LOW);
  if(cont == 0) 
    digitalWrite(omlPin,HIGH);
  else if(cont == oml) 
    digitalWrite(omlPin,LOW);
  if(cont == 0) 
    digitalWrite(oflPin,HIGH);
  else if(cont == ofl) 
    digitalWrite(oflPin,LOW);
}

void setup() {
  
  tfr = 40;//Dereita
  tmr = 40;
  tbr = 40;
  tfl = 70;//Ota dereita
  tml = 70;
  tbl = 70;
  
  ffr = 30;//Dereita
  fmr = 30;
  fbr = 30;
  ffl = 75;//Ota dereita
  fml = 75;
  fbl = 75;

  ofr = 65;//Dereita
  omr = 50;
  obr = 35;
  ofl = 35;//Ota dereita
  oml = 50;
  obl = 65;

  pinMode(tfrPin, OUTPUT);
  pinMode(tmrPin, OUTPUT);
  pinMode(tbrPin, OUTPUT); 
  pinMode(tflPin, OUTPUT);
  pinMode(tmlPin, OUTPUT);
  pinMode(tblPin, OUTPUT);
  
  pinMode(ffrPin, OUTPUT);
  pinMode(fmrPin, OUTPUT);
  pinMode(fbrPin, OUTPUT); 
  pinMode(fflPin, OUTPUT);
  pinMode(fmlPin, OUTPUT);
  pinMode(fblPin, OUTPUT);

  pinMode(ofrPin, OUTPUT);
  pinMode(omrPin, OUTPUT);
  pinMode(obrPin, OUTPUT); 
  pinMode(oflPin, OUTPUT);
  pinMode(omlPin, OUTPUT);
  pinMode(oblPin, OUTPUT);
  
  timer = timerBegin(3, 80, true);
  timerAttachInterrupt(timer, &onTimer, true);
  timerAlarmWrite(timer, 20, true); //20ms gera pwm de 50Hz
  timerAlarmEnable(timer);
  
  Serial.begin(115200);          // make sure your Serial Monitor is also set at this baud rate.
  Dabble.begin("Tiffany");       //set bluetooth name of your device

}

void loop() {
  Dabble.processInput();             //this function is used to refresh data obtained from smartphone.Hence calling this function is mandatory in order to get data properly from your mobile.
  if (GamePad.isUpPressed())
  {
    ffr = 35;
    fml = 70;
    fbr = 35;
    delay(100);
    tfr = 50;
    tbr = 40;
    while(ofr>=40 && oml<=55 && obr>=50)
    {
      ofr--;
      oml++;
      obr--;
      delay(20); 
    }  
    ffr = 50;
    fml = 55;
    fbr = 50;
    delay(100);
    ffl = 70;
    fmr = 35;
    fbl = 70;
    delay(100);
    tfl = 60;
    tbl = 70;
    while(ofr<=50 && oml>=45 && obr<=60)
    {
      ofr++;
      oml--;
      obr++;
      tfr--;
      tbr++;
      delay(20); 
    }
    while(ofl<=60 && omr>=45 && obl<=50)
    {
      ofl++;
      omr--;
      obl++;
      delay(20);
    }
    ffl = 55;
    fmr = 50;
    fbl = 55;
    delay(100);
    ffr = 35;
    fml = 70;
    fbr = 35;
    delay(100);
    while(ofl>=50 && omr<=55 && obl>=40)
    {
      ofl--;
      omr++;
      obl--;
      tfl++;
      tbl--;
      delay(20);
    }
  }
  
  else if (GamePad.isDownPressed())
  {
    ffr = 35;
    fml = 70;
    fbr = 35;
    delay(100);
    tfr = 40;
    tbr = 50;
    while(ofr<=50 && oml>=45 && obr<=60)
    {
      ofr++;
      oml--;
      obr++;
      delay(20); 
    }  
    ffr = 50;
    fml = 55;
    fbr = 50;
    delay(100);
    ffl = 70;
    fmr = 35;
    fbl = 70;
    delay(100);
    tfl = 70;
    tbl = 60;
    while(ofr>=40 && oml<=55 && obr>=50)
    {
      ofr--;
      oml++;
      obr--;
      tfr++;
      tbr--;
      delay(20); 
    }
    while(ofl>=50 && omr<=55 && obl>=40)
    {
      ofl--;
      omr++;
      obl--;
      delay(20);
    }
    ffl = 55;
    fmr = 50;
    fbl = 55;
    delay(100);
    ffr = 35;
    fml = 70;
    fbr = 35;
    delay(100);
    while(ofl<=60 && omr>=45 && obl<=50)
    {
      ofl++;
      omr--;
      obl++;
      tfl--;
      tbl++;
      //if(ffl>=53)
        //ffl--;
      delay(20);
    }
  }
  
    else if (GamePad.isLeftPressed())
  {
    ffr = 35;
    fml = 70;
    fbr = 35;
    delay(100);
    while(ofr>=42 && oml>=47 && obr>=52)
    {
      ofr--;
      oml--;
      obr--;
      delay(20); 
    }  
    ffr = 50;
    fml = 55;
    fbr = 50;
    delay(100);
    ffl = 70;
    fmr = 35;
    fbl = 70;
    delay(100);
    while(ofr<=48 && oml<=53 && obr<=58)
    {
      ofr++;
      oml++;
      obr++;
      delay(20); 
    }
    while(ofl>=52 && omr>=47 && obl>=42)
    {
      ofl--;
      omr--;
      obl--;
      delay(20);
    }
    ffl = 55;
    fmr = 50;
    fbl = 55;
    delay(100);
    ffr = 35;
    fml = 70;
    fbr = 35;
    delay(100);
    while(ofl<=58 && omr<=53 && obl<=48)
    {
      ofl++;
      omr++;
      obl++;
      delay(20);
    }
  }

  else if (GamePad.isRightPressed())
  {
    
    ffr = 35;
    fml = 70;
    fbr = 35;
    delay(100);
    while(ofr<=48 && oml<=53 && obr<=58)
    {
      ofr++;
      oml++;
      obr++;
      delay(20); 
    }  
    ffr = 50;
    fml = 55;
    fbr = 50;
    delay(100);
    ffl = 70;
    fmr = 35;
    fbl = 70;
    delay(100);
    while(ofr>=42 && oml>=47 && obr>=52)
    {
      ofr--;
      oml--;
      obr--;
      delay(20); 
    }
    while(ofl<=58 && omr<=53 && obl<=48)
    {
      ofl++;
      omr++;
      obl++;
      delay(20);
    }
    ffl = 55;
    fmr = 50;
    fbl = 55;
    delay(100);
    ffr = 35;
    fml = 70;
    fbr = 35;
    delay(100);
    while(ofl>=52 && omr>=47 && obl>=42)
    {
      ofl--;
      omr--;
      obl--;
      delay(20);
    }
  }
  
  else if(ffr==35 && fml==70 && fbr==35 && ffl==55 && fmr==50 && fbl==55)
  {
    ofr = 45;
    ofl = 55;
    omr = 50;
    oml = 50;
    obr = 55;
    obl = 45;
    delay(200);
    tfr = 50;
    tfl = 60;
    tmr = 50;
    tml = 60;
    tbr = 50;
    tbl = 60;
    delay(200);
    ffr = 50;
    ffl = 55;
    fmr = 50;
    fml = 55;
    fbr = 50;
    fbl = 55;
    delay(200);
  }
  if (GamePad.isSquarePressed())
  {
  }

  if (GamePad.isCirclePressed())
  {
  }

  if (GamePad.isCrossPressed())
  {
    tbr = tbr - 5; //Dereita
    tmr = tmr - 5;
    tfr = tfr - 5;

    tbl = tbl + 5; //Ota dereita
    tml = tml + 5;
    tfl = tfl + 5;
    
    obr = obr + 5; //Dereita
    omr = omr + 5;
    ofr = ofr + 5;

    obl = obl - 5; //Ota dereita
    oml = oml - 5;
    ofl = ofl - 5;
    
    fbr = fbr - 5; //Dereita
    fmr = fmr - 5;
    ffr = ffr - 5;

    fbl = fbl + 5; //Ota dereita
    fml = fml + 5;
    ffl = ffl + 5;
    delay(200);
  }

  if (GamePad.isTrianglePressed())
  {
    tbr = tbr + 5; //Dereita
    tmr = tmr + 5;
    tfr = tfr + 5;

    tbl = tbl - 5; //Ota dereita
    tml = tml - 5;
    tfl = tfl - 5;
    
    obr = obr - 5; //Dereita
    omr = omr - 5;
    ofr = ofr - 5;

    obl = obl + 5; //Ota dereita
    oml = oml + 5;
    ofl = ofl + 5;
    
    fbr = fbr + 5; //Dereita
    fmr = fmr + 5;
    ffr = ffr + 5;

    fbl = fbl - 5; //Ota dereita
    fml = fml - 5;
    ffl = ffl - 5;
    delay(200);
  }

  if (GamePad.isStartPressed())
  {
    if(ofr==65 && ofl==35 && obr==35 && obl==65)
    {
    tfr = 85;
    tfl = 25;
    tmr = 85;
    tml = 25;
    tbr = 85;
    tbl = 25;
    delay(200);
    ofr = 45;
    ofl = 55;
    omr = 50;
    oml = 50;
    obr = 55;
    obl = 45;
    delay(200);
    ffr = 60;
    ffl = 45;
    fmr = 60;
    fml = 45;
    fbr = 60;
    fbl = 45;
    delay(500);

    ffr = 45;
    delay(200);
    ofr = 45;
    delay(200);
    tfr = 45;
    delay(300);
    
    fmr = 45;
    delay(200);
    omr = 50;
    delay(200);
    tmr = 45;
    delay(300);
    
    fbr = 45;
    delay(200);
    obr = 55;
    delay(200);
    tbr = 45;
    delay(300);
    
    fbl = 60;
    delay(200);
    obl = 45;
    delay(200);
    tbl = 65;
    delay(300);
    
    fml = 60;
    delay(200);
    oml = 50;
    delay(200);
    tml = 65;
    delay(300);
    
    ffl = 60;
    delay(200);
    ofl = 55;
    delay(200);
    tfl = 65;
    delay(300);

    //+5 right & -5 left
    ffr = 50;
    ffl = 55;
    fmr = 50;
    fml = 55;
    fbr = 50;
    fbl = 55;
    delay(500);

    //ajuste das tibias
    ffr = 30;
    delay(300);
    tfr = 45;
    delay(300);
    ffr = 50;
    delay(100);

    fmr = 30;
    delay(300);
    tmr = 45;
    delay(300);
    fmr = 50;
    delay(100);
    
    fbr = 30;
    delay(300);
    tbr = 45;
    delay(300);
    fbr = 50;
    delay(100);
    
    fbl = 75;
    delay(300);
    tbl = 65;
    delay(300);
    fbl = 55;
    delay(100);
    
    fml = 75;
    delay(300);
    tml = 65;
    delay(300);
    fml = 55;
    delay(100);
    
    ffl = 75;
    delay(300);
    tfl = 65;
    delay(300);
    ffl = 55;
    delay(100);
    }
    else
    {
      ofr = 45;
      ofl = 55;
      omr = 50;
      oml = 50;
      obr = 55;
      obl = 45;
      delay(200);
      tfr = 50;
      tfl = 60;
      tmr = 50;
      tml = 60;
      tbr = 50;
      tbl = 60;
      delay(200);
      ffr = 50;
      ffl = 55;
      fmr = 50;
      fml = 55;
      fbr = 50;
      fbl = 55;
      delay(200);
    }
  }

  if (GamePad.isSelectPressed())
  {
    //1º
    ffr = 45;
    ffl = 60;
    fmr = 45;
    fml = 60;
    fbr = 45;
    fbl = 60;
    delay(100);
    //2º
    ffr = 46;
    ffl = 59;
    fmr = 46;
    fml = 59;
    fbr = 46;
    fbl = 59;
    delay(100);
    //3º
    ffr = 42;
    ffl = 63;
    fmr = 42;
    fml = 63;
    fbr = 42;
    fbl = 63;
    delay(100);
    //4º
    ffr = 38;
    ffl = 67;
    fmr = 38;
    fml = 67;
    fbr = 38;
    fbl = 67;
    delay(100);
    //5º
    ffr = 34;
    ffl = 71;
    fmr = 34;
    fml = 71;
    fbr = 34;
    fbl = 71;
    delay(100);
    //6º
    ffr = 30;
    ffl = 75;
    fmr = 30;
    fml = 75;
    fbr = 30;
    fbl = 75;
    delay(500);
    
    tfr = 40;
    tfl = 70;
    tmr = 40;
    tml = 70;
    tbr = 40;
    tbl = 70;
    delay(500);
    
    ofr = 65;
    ofl = 35;
    omr = 50;
    oml = 50;
    obr = 35;
    obl = 65;
    delay(500);
    
    ESP.restart();
  }
}

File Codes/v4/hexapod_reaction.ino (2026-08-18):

#define CUSTOM_SETTINGS
#define INCLUDE_GAMEPAD_MODULE
#include <DabbleESP32.h>
#include <Wire.h>
#include "SparkFun_BNO08x_Arduino_Library.h"
#include <LeggedRobot.h>
 
// --------- I2C addresses ----------
#define BNO_ADDR  0x4B
 
// --------- IMU ----------
BNO08x myIMU;

#define MAX_ANGLE 15.0
const float L1 = 2.53, L2 = 9.0, L3 = 12.16;

Adafruit_PWMServoDriver pwmL = Adafruit_PWMServoDriver(0x40);
Adafruit_PWMServoDriver pwmR = Adafruit_PWMServoDriver(0x41);

// Criacao das patas e do hexapod
RobotLeg LeftFoward    = {&pwmL, 12, 13, 14, 343, 758, 336, 750, 151, -259, L1, L2, L3};
RobotLeg LeftMiddle    = {&pwmL,  4,  5,  6, 312, 727, 296, 710, 174, -239, L1, L2, L3};
RobotLeg LeftBackward  = {&pwmL,  0,  1,  2, 316, 730, 325, 731, 141, -278, L1, L2, L3};

RobotLeg RightFoward   = {&pwmR,  0,  1,  2, 326, -80, 301, -103, 486, 887, L1, L2, L3};
RobotLeg RightMiddle   = {&pwmR,  8,  9, 10, 301,-107, 316,  -92, 503, 919, L1, L2, L3};
RobotLeg RightBackward = {&pwmR, 12, 13, 14, 313, -89, 286, -126, 479, 891, L1, L2, L3};

LegConfig LeftFowardConfig    = {floatxyz{9.30,5.55,0.00}, int3{-45,26,-100}, 0, 0};
LegConfig LeftMiddleConfig    = {floatxyz{0.00,6.50,0.00}, int3{  0,26,-100}, RobotLeg::HALF_POINTS, 0};
LegConfig LeftBackwardConfig  = {floatxyz{-9.5,5.50,0.00}, int3{ 45,26,-100}, 0, 0};

LegConfig RightFowardConfig   = {floatxyz{9.30,-5.55,0.0}, int3{135,26,-100}, RobotLeg::HALF_POINTS, M_PI};
LegConfig RightMiddleConfig   = {floatxyz{0.00,-6.50,0.0}, int3{180,26,-100}, 0, M_PI};
LegConfig RightBackwardConfig = {floatxyz{-9.5,-5.50,0.0}, int3{225,26,-100}, RobotLeg::HALF_POINTS, M_PI};

RobotLeg* hexapodLegs[6] = {&LeftFoward, &LeftMiddle, &LeftBackward, &RightFoward, &RightMiddle, &RightBackward};
LegConfig hexapodConfigs[6] = {LeftFowardConfig, LeftMiddleConfig, LeftBackwardConfig, RightFowardConfig, RightMiddleConfig, RightBackwardConfig};

LeggedRobot robot(hexapodLegs, hexapodConfigs, 6);

void TaskRobot(void *pvParameters);
void TaskCommunication(void *pvParameters);
void TaskIMU(void *pvParameters);
 
void setup() {
  Serial.begin(38400);
  Dabble.begin("Tiffany");
  Serial.println("Tiffany started!");

  // Config PCA9685
  pwmL.begin(); pwmL.setPWMFreq(50);
  pwmR.begin(); pwmR.setPWMFreq(50);

  // Start BNO080 at 0x4B
  if (!myIMU.begin(BNO_ADDR, Wire)) {
    Serial.println("BNO080 not found");
    while (1) delay(10);
  }
  myIMU.enableRotationVector(50);

  delay(2000);
  xTaskCreate(TaskRobot, "robot", 4096, NULL, 1, NULL);
  xTaskCreate(TaskCommunication, "communication", 4096, NULL, 1, NULL);
  xTaskCreate(TaskIMU, "imu", 4096, NULL, 1, NULL);
}

void loop(){}

// State machine variables
int state = 11;
int angleJoystick = 90;
int mode = 0; // 0 - Omnidirecional, 1 - Rotacional

void TaskRobot(void *pvParameters) {
  int k = 0;
  int totalPoints = RobotLeg::TOTAL_POINTS;
  for (;;) {
    // High handshake
    if(state == 1){
        totalPoints = 50;
        int3 angles = {-10,-10,0};
        // robot.handShake(k,3,totalPoints);
        robot.highHandShake(k,3,angles,totalPoints);
        #if DEBUG_SIMULADOR
          robot.sendAngles(k);
        #endif
        if (k < (totalPoints/2)){
          k++;
        }
        vTaskDelay(pdMS_TO_TICKS(2));
    }
    // Wiggle
    else if(state == 2){
        int3 angles = robot.circularRollPitchYaw(k, 10);
        robot.bodyTilt(angles);
        #if DEBUG_SIMULADOR
          robot.sendAngles(k);
        #endif         
        if (k == LeggedRobot::TOTAL_CIRCULAR_POINTS - 1){
          k = 0;
        }
        else{
          k++;
        }
        vTaskDelay(pdMS_TO_TICKS(20));
    }
    // mode 0 - Omnidirectional walk, mode 1 - Circular walk, mode 2 - Circular walk with IMU reaction
    else if(state == 3){
      float angle = joystickToInt(angleJoystick,5);
      if (mode == 0){
        float angle_rad = angle*M_PI/180.0;
        k = robot.walk(k,angle_rad);
      }
      else if (mode == 1){
        k = robot.circularWalk(k,angle);
      }
      else{
        int3 anglesint3 = int3(robot.poseAngles);
        k = robot.reactCircularWalk(k,angle,anglesint3);
      }
      #if DEBUG_SIMULADOR
        robot.sendAngles(k);
      #endif         
      vTaskDelay(pdMS_TO_TICKS(20));
    }
    // Start robot
    else if(state == 9){
        robot.start();
        state = 0;
        vTaskDelay(pdMS_TO_TICKS(500));
    }
    // Shutdown robot
    else if(state == 10){
        robot.shutdown();
        state = 11;
        vTaskDelay(pdMS_TO_TICKS(1));
    }
    // Idle position
    else if(state == 0){
      k = 0;
      // Idle reacting to IMU
      if (mode == 2){
        int3 anglesint3 = int3(robot.poseAngles);
        robot.idle(anglesint3);
      }
      // Idle straight position
      else{
        robot.idle();
      }
      #if DEBUG_SIMULADOR
        robot.sendAngles(k);
      #endif     
      vTaskDelay(pdMS_TO_TICKS(15));
    }
    else{
      vTaskDelay(pdMS_TO_TICKS(10));
    }
  }
}

void TaskCommunication(void *pvParameters) {
  for (;;) {
    Dabble.processInput();
    // Commands after start
    if (state != 11){
      // Circular walk mode
      if (GamePad.isRightPressed()||GamePad.isLeftPressed()||GamePad.isCrossPressed()){
        mode = 1;
      }
      // Omnidirectional walk mode
      if (GamePad.isUpPressed()||GamePad.isDownPressed()){
        mode = 0;
      }
      // Tilt reaction with IMU mode
      if (GamePad.isSquarePressed()){
        mode = 2;
      }
      // High handshake while pressing
      if (GamePad.isCirclePressed()){
        state = 1;
      }
      // Wiggle while pressing
      else if(GamePad.isTrianglePressed()){
        state = 2;
      }
      // Walk
      else if(GamePad.getRadius() > 2){
        angleJoystick = GamePad.getAngle();
        state = 3;
      }
      // Shutdown robot
      else if(GamePad.isSelectPressed()){
        state = 10;
      }
      // Idle
      else{
        state = 0;
      }
    }
    // Before start
    else{
      // Start command
      if(GamePad.isStartPressed()){
        state = 9;
      }
    }
    vTaskDelay(pdMS_TO_TICKS(20));   
  }
}
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

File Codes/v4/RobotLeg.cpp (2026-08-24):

#include "RobotLeg.h"

// =====================================================
// float3 / int3
// =====================================================

int3::int3(const float3& values) {
    coxa = (int)values.coxa;
    femur = (int)values.femur;
    tibia = (int)values.tibia;
}

float3::float3(const int3& values) {
    coxa = (float)values.coxa;
    femur = (float)values.femur;
    tibia = (float)values.tibia;
}


// =====================================================
// Conversions
// =====================================================

int radToDegree(float angles_rad) {
    return int(angles_rad * 180.0 / M_PI);
}

int3 radToDegree(float3 angles_rad) {
    return {
        int(angles_rad.coxa * 180.0 / M_PI),
        int(angles_rad.femur * 180.0 / M_PI),
        int(angles_rad.tibia * 180.0 / M_PI)
    };
}

float3 degreeToRad(int3 angles) {
    return {
        float(angles.coxa) * M_PI / 180.0,
        float(angles.femur) * M_PI / 180.0,
        float(angles.tibia) * M_PI / 180.0
    };
}


// =====================================================
// Joystick
// =====================================================

float joystickToRad(int joystickAngle) {
    float angle_rad = (float(joystickAngle) - 90.0) * M_PI / 180.0;

    while (angle_rad > M_PI)
        angle_rad -= 2 * M_PI;

    while (angle_rad < -M_PI)
        angle_rad += 2 * M_PI;

    return angle_rad;
}


int joystickToInt(int joystickAngle, int deltaAngle) {
    int angle = joystickAngle - 90;

    while (angle > 180)
        angle -= 360;

    while (angle < -180)
        angle += 360;

    if (abs(angle - 180) <= deltaAngle || abs(angle + 180) <= deltaAngle) {
        return 180;
    }

    if (abs(angle - 90) <= deltaAngle * 4) {
        return 90;
    }

    if (abs(angle + 90) <= deltaAngle * 4) {
        return -90;
    }

    if (abs(angle) <= deltaAngle) {
        return 0;
    }

    return angle;
}


// =====================================================
// Construtor
// =====================================================

RobotLeg::RobotLeg(
    Adafruit_PWMServoDriver* pwm,
    int pinCoxa,
    int pinFemur,
    int pinTibia,
    int CMIN,
    int CMAX,
    int FMIN,
    int FMAX,
    int TMIN,
    int TMAX,
    float L1,
    float L2,
    float L3
) {

    this->pwm = pwm;

    this->pins = {pinCoxa, pinFemur, pinTibia};

    this->angles = {-1, -1, -1};

    this->footPosition = {0.0f, 0.0f, 0.0f};

    this->LIMMIN = {CMIN, FMIN, TMIN};
    this->LIMMAX = {CMAX, FMAX, TMAX};

    this->L1 = L1;
    this->L2 = L2;
    this->L3 = L3;

    P0[0] = P0[1] = 0.0;
    P1[0] = P1[1] = 0.0;
    P2[0] = P2[1] = 0.0;
    P3[0] = P3[1] = 0.0;
}


// =====================================================
// Servo control
// =====================================================

void RobotLeg::move(int angCoxa, int angFemur, int angTibia) {
    if (this->angles.coxa != angCoxa) {
        this->angles.coxa = angCoxa;
        int pulse = map(this->angles.coxa, 0, 180, LIMMIN.coxa, LIMMAX.coxa);
        pwm->setPWM(pins.coxa, 0, pulse);
    }

    if (this->angles.femur != angFemur) {
        this->angles.femur = angFemur;
        int pulse = map(this->angles.femur, 0, 180, LIMMIN.femur, LIMMAX.femur);
        pwm->setPWM(pins.femur, 0, pulse);
    }

    if (this->angles.tibia != angTibia) {
        this->angles.tibia = angTibia;
        int pulse = map(this->angles.tibia, 0, 180, LIMMIN.tibia, LIMMAX.tibia);
        pwm->setPWM(pins.tibia, 0, pulse);
    }
}

bool RobotLeg::moveSoft(int angCoxa, int angFemur, int angTibia, int step) {
    bool stopped = true;

    if (this->angles.coxa != angCoxa) {
        stopped = false;

        if (abs(this->angles.coxa - angCoxa) < step)
            this->angles.coxa = angCoxa;
        else if (this->angles.coxa < angCoxa)
            this->angles.coxa += step;
        else
            this->angles.coxa -= step;

        int pulse = map(this->angles.coxa, 0, 180, LIMMIN.coxa, LIMMAX.coxa);
        pwm->setPWM(pins.coxa, 0, pulse);
    }

    if (this->angles.femur != angFemur) {
        stopped = false;

        if (abs(this->angles.femur - angFemur) < step)
            this->angles.femur = angFemur;
        else if (this->angles.femur < angFemur)
            this->angles.femur += step;
        else
            this->angles.femur -= step;

        int pulse = map(this->angles.femur, 0, 180, LIMMIN.femur, LIMMAX.femur);
        pwm->setPWM(pins.femur, 0, pulse);
    }

    if (this->angles.tibia != angTibia) {
        stopped = false;

        if (abs(this->angles.tibia - angTibia) < step)
            this->angles.tibia = angTibia;
        else if (this->angles.tibia < angTibia)
            this->angles.tibia += step;
        else
            this->angles.tibia -= step;

        int pulse = map(this->angles.tibia, 0, 180, LIMMIN.tibia, LIMMAX.tibia);
        pwm->setPWM(pins.tibia, 0, pulse);
    }

    return stopped;
}

void RobotLeg::moveToInitialPosition() {
    int3 angles = inverseKinematics(this->footPosition);
    // this->move(angles.coxa, angles.femur, angles.tibia);
    this->moveSoft(angles.coxa, angles.femur, angles.tibia, 1);
}

void RobotLeg::shutdown() {
    // pwm->setPin(pins.coxa, 0, 4096);
    // pwm->setPin(pins.femur, 0, 4096);
    // pwm->setPin(pins.tibia, 0, 4096);
}

// =====================================================
// Kinematics
// =====================================================

floatxyz RobotLeg::directKinematics(int3 angles){
    float3 angles_rad = degreeToRad(angles);
    floatxyz xyz;
                                                                                                                                                                                                  
    xyz.x = -sin(angles_rad.coxa)*(this->L1 + this->L3*cos(angles_rad.femur + angles_rad.tibia) + this->L2*cos(angles_rad.femur));
    xyz.y = cos(angles_rad.coxa)*(this->L1 + this->L3*cos(angles_rad.femur + angles_rad.tibia) +this->L2*cos(angles_rad.femur));
    xyz.z = this->L3*sin(angles_rad.femur + angles_rad.tibia) + this->L2*sin(angles_rad.femur);
    return xyz;
}

int3 RobotLeg::inverseKinematics(floatxyz xyz){
    float3 angles_rad;
    float y_prime = sqrt(xyz.x * xyz.x + xyz.y * xyz.y) - this->L1;
    float L = sqrt(xyz.z * xyz.z + y_prime * y_prime);

    float alpha = acos(constrain((this->L2 * this->L2 + this->L3 * this->L3 - L * L) / (2 * this->L2 * this->L3), -1.0f, 1.0f));
    float beta = acos(constrain((L * L + this->L2 * this->L2 - this->L3 * this->L3) / (2 * L * this->L2), -1.0f, 1.0f));
    
    angles_rad.tibia = -M_PI + alpha;
    angles_rad.coxa = -atan2(xyz.x, xyz.y);
    angles_rad.femur = beta + atan2(xyz.z, y_prime);
    return radToDegree(angles_rad);
}

// =====================================================
// Trajectories
// =====================================================
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

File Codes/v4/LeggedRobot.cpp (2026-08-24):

#include "LeggedRobot.h"

// =====================================================
// Math functions
// =====================================================

floatxyz coordLegToBody(floatxyz legPosition, float installedAngle_rad, floatxyz coxa){
    floatxyz xyz;
    xyz.x = cos(installedAngle_rad)*legPosition.x - sin(installedAngle_rad)*legPosition.y + coxa.x;
    xyz.y = sin(installedAngle_rad)*legPosition.x + cos(installedAngle_rad)*legPosition.y + coxa.y;
    xyz.z = legPosition.z + coxa.z;
    return xyz;
}

floatxyz coordBodyToLeg(floatxyz bodyPosition, float installedAngle_rad, floatxyz coxa){
    floatxyz xyz = bodyPosition - coxa;
    xyz.x = cos(-installedAngle_rad)*(bodyPosition.x - coxa.x) - sin(-installedAngle_rad)*(bodyPosition.y - coxa.y);
    xyz.y = sin(-installedAngle_rad)*(bodyPosition.x - coxa.x) + cos(-installedAngle_rad)*(bodyPosition.y - coxa.y);
    xyz.z = bodyPosition.z - coxa.z;
    return xyz;
}

floatxyz Rotation3d(floatxyz point, int3 angles){
    floatxyz rotPoint;
    float3 angles_rad = degreeToRad(angles);
    float roll = angles_rad.coxa;
    float pitch = angles_rad.femur;
    float yaw = angles_rad.tibia;
    rotPoint.x = point.x*cos(pitch)*cos(yaw) + point.y*(cos(yaw)*sin(pitch)*sin(roll) - cos(roll)*sin(yaw)) + point.z*(sin(roll)*sin(yaw) + cos(roll)*cos(yaw)*sin(pitch));
    rotPoint.y = point.x*cos(pitch)*sin(yaw) + point.y*(cos(roll)*cos(yaw) + sin(pitch)*sin(roll)*sin(yaw)) + point.z*(cos(roll)*sin(pitch)*sin(yaw) - cos(yaw)*sin(roll));
    rotPoint.z = -point.x*sin(pitch) + point.y*cos(pitch)*sin(roll) + point.z*cos(pitch)*cos(roll);
    return rotPoint;
}

LeggedRobot::LeggedRobot(RobotLeg** robotlegs, LegConfig* config, int numLegs) {
    this->robotlegs = robotlegs;
    this->numLegs = numLegs;
    for (int i = 0; i < numLegs; i++) {
        this->config[i] = config[i];
    }
    poseAngles = {0.0, 0.0, 0.0};
}

// =====================================================
// Legs access
// =====================================================

RobotLeg* LeggedRobot::robotleg(int index) {
    if (index < 0 || index >= numLegs)
        return nullptr;
    return robotlegs[index];
}

// =====================================================
// Robot initialization
// =====================================================

void LeggedRobot::start(){
    int totalPoints = 100;
    int halfPoints = totalPoints/2;
    floatxyz xyzStart[MAX_LEGS];
    
    // Move the legs to coccum position and store the correct start foot position xyz
    for (int i = 0; i < numLegs; i++) {
        int installedAngle = radToDegree(config[i].installedAngle_rad);
        int3 initiAngles = {config[i].initialAngles.coxa - installedAngle,config[i].initialAngles.femur,config[i].initialAngles.tibia};
        int3 anglesStart = {initiAngles.coxa,90,-135};
        xyzStart[i] = robotlegs[i]->initializeLeg(anglesStart);
        robotlegs[i]->calculateFootPosition(initiAngles);
    }
    delay(1000);
    #if DEBUG_SIMULADOR
        this->sendAngles(0);
    #endif
    
    // Horizontal move to (footPosition_x,footPosition_y,xyzStart_z)
    int k = 0;
    while (k < halfPoints) {
        int3 angles[MAX_LEGS];
        for (int i = 0; i < numLegs; i++) {
            floatxyz xyz = robotlegs[i]->legBezierTrajetory(xyzStart[i], k, 0, robotlegs[i]->footPosition.x - xyzStart[i].x, robotlegs[i]->footPosition.y - xyzStart[i].y, 0, totalPoints);
            angles[i] = robotlegs[i]->inverseKinematics(xyz);
        }
        for (int i = 0; i < numLegs; i++) {
            robotlegs[i]->move(angles[i].coxa, angles[i].femur, angles[i].tibia);
        }
        #if DEBUG_SIMULADOR
            this->sendAngles(k);
        #endif
        k++;
        delay(20);
    }
    delay(1000);
    
    // Update foot position before moving down to the ground
    for (int i = 0; i < numLegs; i++) {
        xyzStart[i] = {robotlegs[i]->footPosition.x,robotlegs[i]->footPosition.y,xyzStart[i].z};
    }
    
    // Move the legs to start foot position xyz
    k = 0;
    while (k < halfPoints){
        int3 angles[MAX_LEGS];
        for (int i = 0; i < numLegs; i++) {
            floatxyz xyz = robotlegs[i]->legBezierTrajetory(xyzStart[i], k, 0, 0, 0, robotlegs[i]->footPosition.z - xyzStart[i].z, totalPoints);
            angles[i] = robotlegs[i]->inverseKinematics(xyz);
        }
        for (int i = 0; i < numLegs; i++) {
            robotlegs[i]->move(angles[i].coxa, angles[i].femur, angles[i].tibia);
        }
        #if DEBUG_SIMULADOR
            this->sendAngles(k);
        #endif           
        k++;
        delay(20);
    }
}

void LeggedRobot::shutdown(){
    int totalPoints = 100;
    int halfPoints = totalPoints/2;
    floatxyz xyzStart[MAX_LEGS];

    // Store the start foot position xyz
    for (int i = 0; i < numLegs; i++) {
        int installedAngle = radToDegree(config[i].installedAngle_rad);
        int3 anglesStart = {config[i].initialAngles.coxa - installedAngle,90,-135};
        xyzStart[i] = robotlegs[i]->directKinematics(anglesStart);
    }
    #if DEBUG_SIMULADOR
        this->sendAngles(0);
    #endif

    // Move up the legs so the robot could lay down (footPosition_x,footPosition_y,xyzStart_z)
    int k = 0;
    while (k < halfPoints){
        int3 angles[MAX_LEGS];
        for (int i = 0; i < numLegs; i++) {
            floatxyz xyz = robotlegs[i]->legBezierTrajetory(robotlegs[i]->footPosition, k, 0, 0, 0, xyzStart[i].z - robotlegs[i]->footPosition.z, totalPoints);
            angles[i] = robotlegs[i]->inverseKinematics(xyz);
        }
        for (int i = 0; i < numLegs; i++) {
            robotlegs[i]->move(angles[i].coxa, angles[i].femur, angles[i].tibia);
        }
        #if DEBUG_SIMULADOR
            this->sendAngles(k);
        #endif           
        k++;
        delay(20);
    }
    delay(1000);
    
    // Store the coccum foot position xyz
    floatxyz xyzCoccum[MAX_LEGS];
    for (int i = 0; i < numLegs; i++) {
        xyzCoccum[i] = {robotlegs[i]->footPosition.x, robotlegs[i]->footPosition.y, xyzStart[i].z};
    }
    #if DEBUG_SIMULADOR
        this->sendAngles(0);
    #endif       

    // Move the legs to coccum foot position
    k = 0;
    while (k < halfPoints){
        int3 angles[MAX_LEGS];
        for (int i = 0; i < numLegs; i++) {
            floatxyz xyz = robotlegs[i]->legBezierTrajetory(xyzCoccum[i], k, 0, xyzStart[i].x - robotlegs[i]->footPosition.x, xyzStart[i].y - robotlegs[i]->footPosition.y, 0, totalPoints);
            angles[i] = robotlegs[i]->inverseKinematics(xyz);
        }
        for (int i = 0; i < numLegs; i++) {
            robotlegs[i]->move(angles[i].coxa, angles[i].femur, angles[i].tibia);
        }
        #if DEBUG_SIMULADOR
            this->sendAngles(k);
        #endif           
        k++;
        delay(20);
    }

    // Shutdown legs
    for (int i = 0; i < numLegs; i++) {
        robotlegs[i]->shutdown();
    }
}
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

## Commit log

2021-12-20 Add files via upload
    Peças 3d em STL
    [TIFFANY_BODY_DOWN.STL, TIFFANY_BODY_UP.STL, TIFFANY_FEMUR_BACK.STL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]
2022-05-20 código de controle de movimento da Tiffany
    Código de comando de andar pra frente, andar pra trás e girar no seu próprio eixo
2022-08-23 código de controle de movimento (otimizado)
    Código de andar pra frente, pra trás, girar e dançar. Utilizando uma biblioteca autoral.
2022-08-23 Arquivos utilizados
    Arquivos utilizados para elaboração do Hexapod Tiffany
2025-04-30 Update 30/04/2025
    Alterado para gerar a trajetória enquanto anda.
2025-05-01 Update 01/05/2025
    Adicionada a função de girar no próprio eixo ou enquanto anda. Ainda não testada
2025-05-01 Update 01/05/2025c
    Adicionei mais uma forma de ripple. Tenho que testar as duas
2025-05-02 Update 02/05/2025
    Adicionado o mover pata para uma posição específica. No exemplo, 10cm pra frente e 10cm pra cima (tipo subir um degrau).
2025-11-04 Update fmt.Println message from 'Hello' to 'Goodbye'
2025-11-05 Change device name from 'Scarlet' to 'Tiffany'
2025-11-07 Add motor calibration section to README
    Added a section on motor calibration using the CALIBRADOR DE MOTORES, detailing the calibration process and linking to relevant resources.
2025-11-10 Update print statement from 'Hello' to 'Goodbye'
2025-12-01 Update leg parameters for hexapod configuration
